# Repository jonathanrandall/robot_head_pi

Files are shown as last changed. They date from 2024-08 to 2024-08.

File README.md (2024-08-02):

# robot_head_pi
making a robot head with a raspberry pi insi
__Poppy Robot Project files__ 
[Poppy Robot Head stls from the poppy opens source project](https://github.com/poppy-project/Poppy-eva-head-design) <br/>

### Parts list:

- __Servo and servo mount__ 
[Cheap Ali express servos](https://www.aliexpress.com/w/wholesale-servo-25kg.html?spm=a2g0o.productlist.search.0)  and 
[servo pan tilt](https://www.aliexpress.com/w/wholesale-servo-pan-tilt-MG995-MG996.html?spm=a2g0o.productlist.search.0) <br/>
- __Raspberry Pi 4__ <br/>
- __90 degree USB C adapter to power pi__
[90 Degree Right Angle USB-C Male to USB-C Female Adapter](https://www.amazon.com.au/dp/B0B2NJ3P3L) <br/>
- __Stereo Camera__
I used [this one](https://www.amazon.com.au/Synchronized-Stereo-USB-Camera-Industrial/dp/B07R8LQKV4) from Amazon but shop around.<br/>
- __Arducam TOF camera__ <br/>
- __breadboard__ (just broke off the side for the 5v and earth rail) <br/>
- __perf board__ <br/>
- __2 x white leds__ (but you can use any colour you like) <br/>
- __2 x 220 ohm resistors__
- __tiny cylinder magnets__ I used these ones [from Amazon](https://www.amazon.com.au/dp/B0CM3KX5BC)

### Instructions
#### Step 1:
Mound the stereo camera, the time of flight camera and the leds on the pef board. 
The LEDs are should be in series with 220 ohm resistors and connected to pins 17 and 26 on the pi. I use 220 ohms because the pi gives 3.3 volts. Also, I drilled 2.5mm holes to mount the electronics on the perf board.
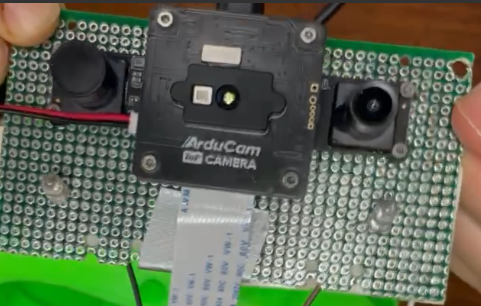
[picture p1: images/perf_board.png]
perf board


#### Step 2:
Print the following three robot head pieces from the Poppy Robot Project files listed above. [Poppy Robot Head](https://github.com/poppy-project/Poppy-eva-head-design) <br/>
__The work for this was done by 3 students of the ENSAM Bachelor of technology at Bordeaux, France: Damien MARTY, Clément GEA and Éléa CHARPNTIER, under the supervison of Jean-Luc CHARLES and Cécile DELARUE, professors at ENSAM Bordeaux.__ I have included the STL files in this repo (in the directory STL), just incase they become unavaiable on the original repo. <br/>
1. The eva_head_frontBottom
2. The head_RPi4Support
3. The head_top-part

They also provide some connectors to attach the tft for the face, but I'm using a pef board instead of a tft, so I just used hot glue. 

#### Step 3:
This is where my design differs from the original design.
Print the servo_head_connection-Body_v2.stl file. This is used to connect the head to the serov pan-tilt. I've also included the freecad file incase you want to adjust the position of the holes. It uses m2 screws. The original project has the head mounted directly to dynamixel servos, but the dynamixel servos were a bit expensive for me, so I went with the cheap ones. Although, with servos you do get what you pay for.
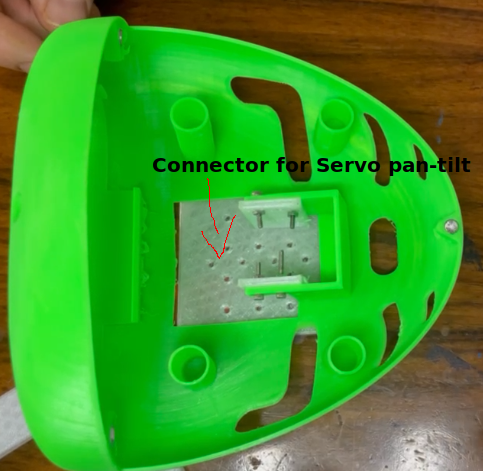
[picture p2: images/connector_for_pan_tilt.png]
connector for pan tilt


### Step 4:
Build the servo pan-tilt. See for example [https://youtu.be/3_fsS4YQ5Aw?si=ct7GD8LKidqGTTAt](https://youtu.be/3_fsS4YQ5Aw?si=ct7GD8LKidqGTTAt)

### Step 5:
Assemble printed files and push magnets into divets (see steps in original project as well). 
1. Connect the +ve of the LED & resistors to pins 17 and 26 of the pi and the -ve to earth. I soldered on some dupont female jumper wires.
2. Connect the servo pan tilt to the bottom of the head.
3. Connect the servo data (middle) wires to pins 18 and 27 of the pi.
4. Connect the servo +ve and -ve to the plus 5v and earth on the breadboard rail (see photo).
5. Connect the earth of the breadboard rail to one of the earths of the pi.
6. Place the perfboard in the face opening of the printed front of the head. You can cut this down to size. I used hot glue for this.
7. Connect the Arducam TOF camera to the pi camera input.
8. Connect the stereo camera to the usb pi input.

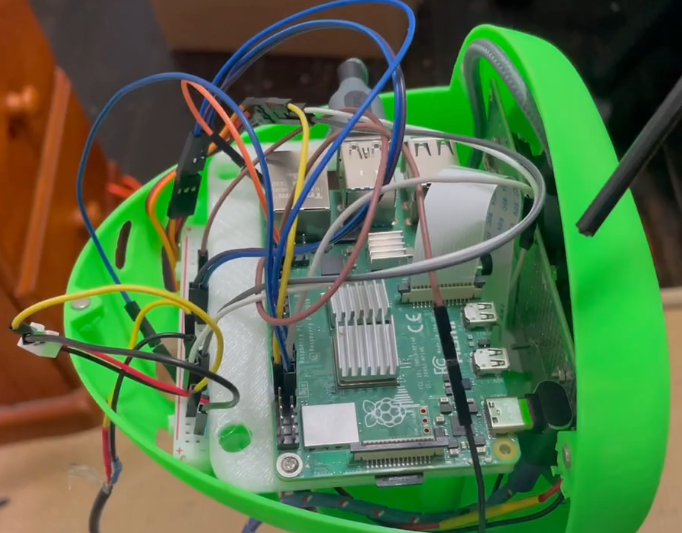
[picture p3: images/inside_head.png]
inside the head


### Step 6:
Put the back on and mount on neck. I used a piece of actobotics channel with a pillow mount that I had lying around. This has since been replaced by U-channel, which you can get from serocity or gobilda. But you can just use whatever you have lying around, whether it's an old piece of aluminium extrusion from a 3d printer or even a chari leg.

### Step 7:
Get the code running.
1. Install the ArducamDepthCamera. If you are on bookwork, you should do this in a virtual environment. To get the camera working see Arducam getting started [https://docs.arducam.com/Raspberry-Pi-Camera/Tof-camera/Getting-Started/](https://docs.arducam.com/Raspberry-Pi-Camera/Tof-camera/Getting-Started/) and
[Arducam github](https://github.com/ArduCAM/Arducam_tof_camera)
2. Note, for the getting started code from Arducam, the index of the camera is set to 0. Since we are using two cameras we need to find the index at run time. There is a function in my python code for this.
3. To run my code, make sure the python file ```robot_head.py``` and the html file ```index.html``` are in the same directory.
4. Since the code serves a webpage, you need to run with sudo, but for some reason, at least for me, I had to qualify the python3 command with the full path of the virtual environment. So I had to type ```sudo path/to/venv/python3 robot_head.py```
5. Go to the pi ip in your browser. I tested this from a computer and a tablet but not a smart phone. You can find the ip by typing ifconfig, or you can just enter the piname.local.

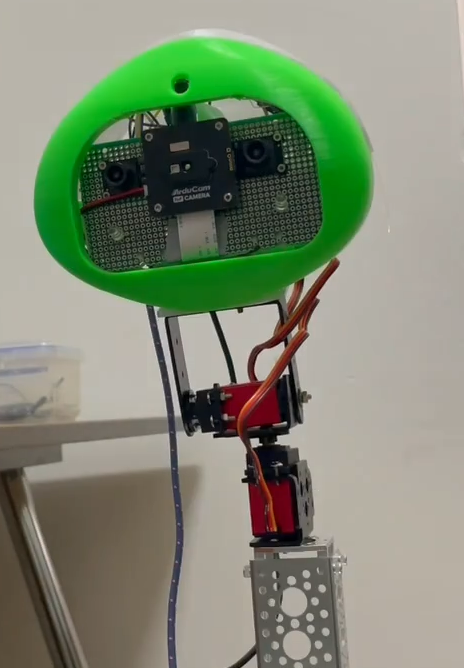
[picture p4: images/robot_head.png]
pi head


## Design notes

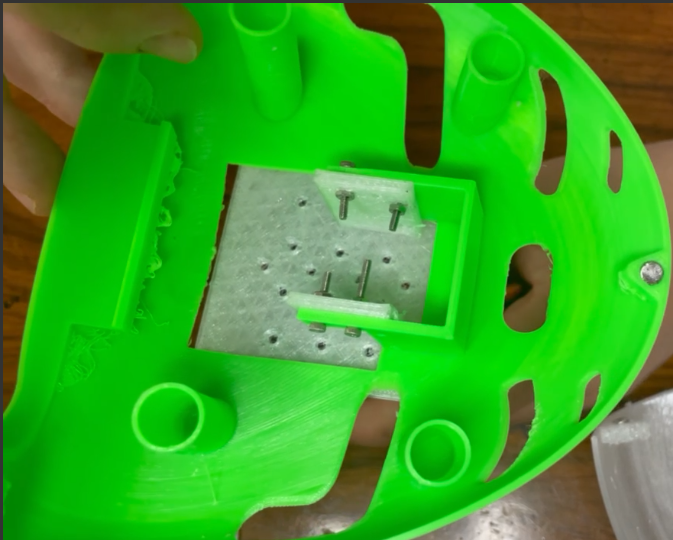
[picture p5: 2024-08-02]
images/Screenshot.png

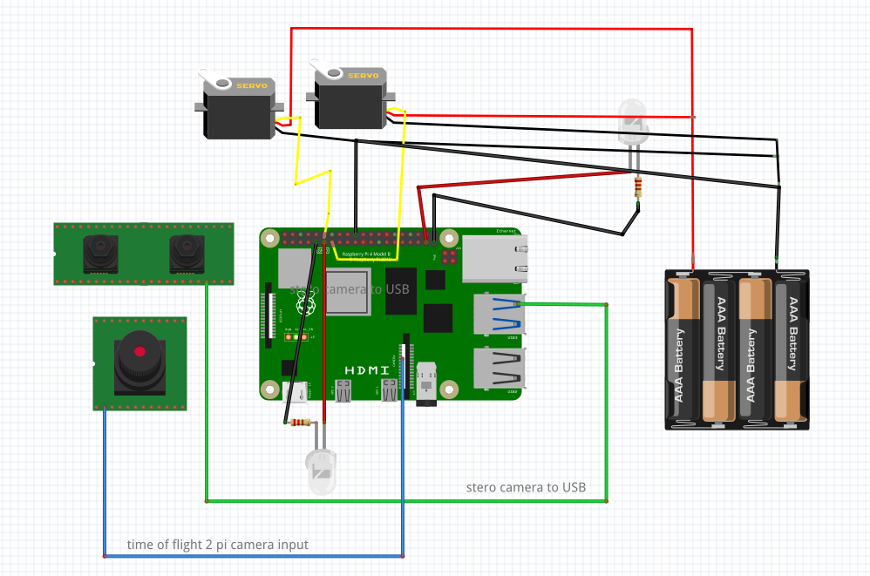
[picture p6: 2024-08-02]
circuit_diagrams/fritzing_circuit.png

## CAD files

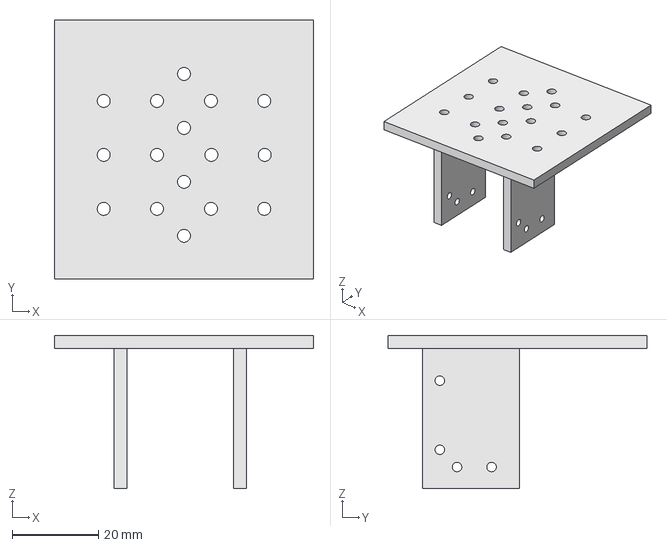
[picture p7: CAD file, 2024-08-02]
servo_mount_3d_print/servo_head_connection.FCStd
60.0 x 60.0 x 35.5 mm

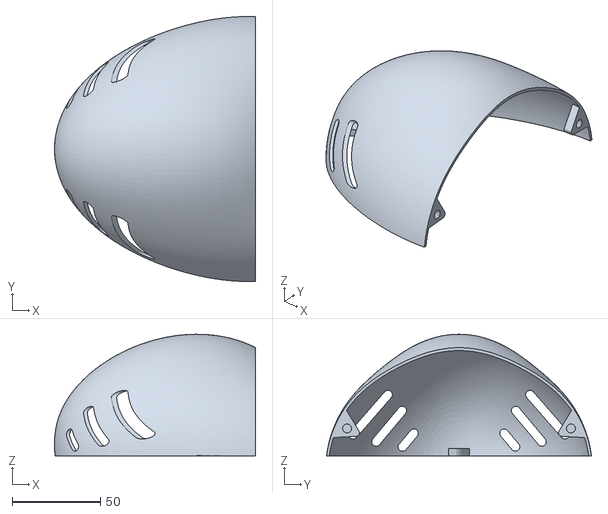
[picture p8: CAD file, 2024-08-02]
servo_mount_3d_print/STL/eva_head_top-part.stl
114.1 x 150.3 x 68.9

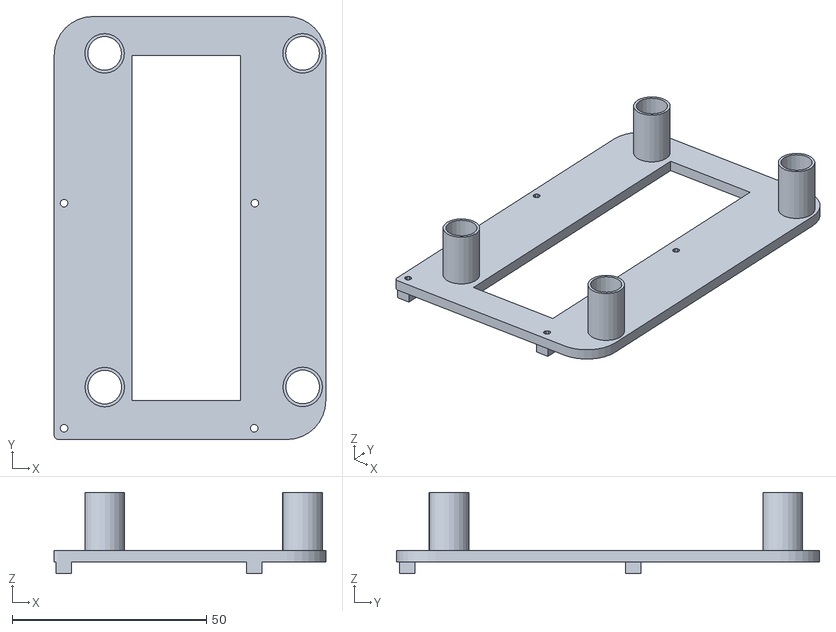
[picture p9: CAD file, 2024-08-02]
servo_mount_3d_print/STL/eva_head_RPi4Support.stl
70.0 x 109.0 x 21.0

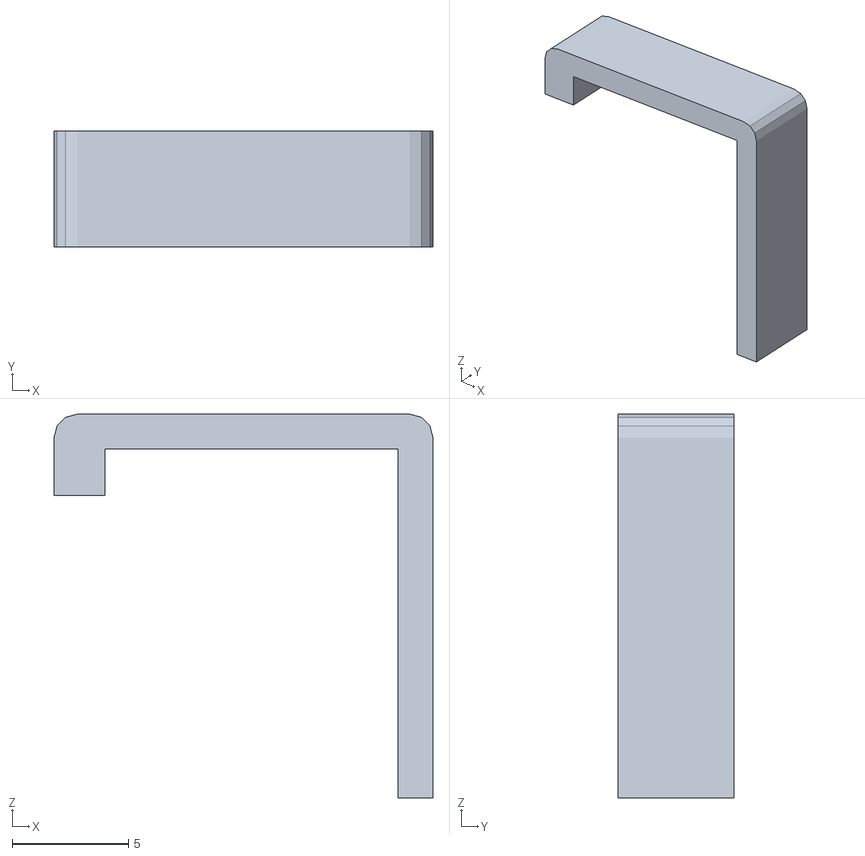
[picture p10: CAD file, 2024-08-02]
servo_mount_3d_print/STL/eva_head_lock-part.stl
16.3 x 5.00 x 16.5

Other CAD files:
servo_mount_3d_print/servo_head_connection-Body_v2.stl

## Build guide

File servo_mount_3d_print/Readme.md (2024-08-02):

The STL directory contains the files from the [eva-head poppy robot project](https://github.com/poppy-project/Poppy-eva-head-design).

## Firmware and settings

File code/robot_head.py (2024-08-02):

from http.server import BaseHTTPRequestHandler, HTTPServer
from socketserver import ThreadingMixIn
import cv2
import threading
import time
from collections import deque
import RPi.GPIO as GPIO
import urllib.parse
import sys

import ArducamDepthCamera as ac
import numpy as np


MAX_DISTANCE = 4

# Set up GPIO
LED_PIN = 17
LED_PIN2 = 26
SERVO_PIN_HORIZONTAL = 27
SERVO_PIN_VERTICAL = 18

GPIO.setmode(GPIO.BCM)
# GPIO.cleanup(LED_PIN)
GPIO.setup(LED_PIN, GPIO.OUT)
GPIO.setup(LED_PIN2, GPIO.OUT)
GPIO.setup(SERVO_PIN_HORIZONTAL, GPIO.OUT)
GPIO.setup(SERVO_PIN_VERTICAL, GPIO.OUT)

GPIO.output(LED_PIN, GPIO.LOW)
GPIO.output(LED_PIN2, GPIO.LOW)

# Set up PWM for servo control
servo_horizontal = GPIO.PWM(SERVO_PIN_HORIZONTAL, 50)  # 50Hz PWM frequency
servo_vertical = GPIO.PWM(SERVO_PIN_VERTICAL, 50)      # 50Hz PWM frequency
servo_horizontal.start(0)
servo_vertical.start(0)
import subprocess

# cam = ac.ArducamCamera()
# if cam.open(ac.TOFConnect.CSI,0) != 0 :
#     print("initialization failed")
# if cam.start(ac.TOFOutput.DEPTH) != 0 :
#     print("Failed to start camera")
# cam.setControl(ac.TOFControl.RANG,MAX_DISTANCE)
# frame_tmp = cam.requestFrame(200)
# depth_buf = frame_tmp.getDepthData()
# amplitude_buf = frame_tmp.getAmplitudeData()
# cam.releaseFrame(frame_tmp)
# amplitude_buf*=(255/1024)
# amplitude_buf = np.clip(amplitude_buf, 0, 255)
# result_image = process_frame(depth_buf,amplitude_buf)
# cv2.imshow("preview",result_image)

# key = cv2.waitKey(1)
# if key == ord("q"):
#     exit_ = True
#     cam.stop()
#     cam.close()
    
def process_frame(depth_buf: np.ndarray, amplitude_buf: np.ndarray) -> np.ndarray:
        
    depth_buf = np.nan_to_num(depth_buf)

    amplitude_buf[amplitude_buf<=7] = 0
    amplitude_buf[amplitude_buf>7] = 255

    depth_buf =(1 - (depth_buf/MAX_DISTANCE)) * 255
    depth_buf = np.clip(depth_buf, 0, 255)
    result_frame = depth_buf.astype(np.uint8)  & amplitude_buf.astype(np.uint8)
    return result_frame 
class ArduCamCam(threading.Thread):
    def __init__(self):
        threading.Thread.__init__(self)
        cam = ac.ArducamCamera()
        camIDx = int(find_webcam_index("unicam"))
        if cam.open(ac.TOFConnect.CSI,camIDx) != 0 :
            print("initialization failed")
        if cam.start(ac.TOFOutput.DEPTH) != 0 :
            print("Failed to start camera")
        cam.setControl(ac.TOFControl.RANG,MAX_DISTANCE)
        self.cam = cam
        self.running = True
        self.frame_queue = deque(maxlen=1)

    def run(self):
        while self.running:
            frame = self.cam.requestFrame(200)
            
            if frame is not None:
                depth_buf = frame.getDepthData()
                amplitude_buf = frame.getAmplitudeData()
                self.cam.releaseFrame(frame)

                amplitude_buf *= (255 / 1024)
                amplitude_buf = np.clip(amplitude_buf, 0, 255)
                result_image = process_frame(depth_buf, amplitude_buf)
                
                ret, jpeg = cv2.imencode('.jpg', result_image)
                if ret:
                    self.frame_queue.append(jpeg.tobytes())
                else:
                    print("Failed to encode frame as JPEG")
            else:
                print("Failed to deque buffer")
            
            time.sleep(0.01)

    def get_frame(self):
        if self.frame_queue:
            return self.frame_queue[-1]
        else:
            return None

    def stop(self):
        self.running = False
        self.cam.stop()
        self.cam.close()



def find_webcam_index(device_name):
    command = "v4l2-ctl --list-devices"
    output = subprocess.check_output(command, shell=True, text=True)
    devices = output.split('\n\n')
    
    for device in devices:
        if device_name in device:
            lines = device.split('\n')
            for line in lines:
                if "video" in line:
                    parts = line.split()
                    for part in parts:
                        if part.startswith('/dev/video'):
                            print(part)
                            return (part[10:])


def set_servo_angle(servo, angle):
    duty_cycle = angle / 18 + 2
    # GPIO.output(servo, True)
    servo.ChangeDutyCycle(duty_cycle)
    time.sleep(0.5)
    # GPIO.output(servo, False)
    servo.ChangeDutyCycle(0)

# Camera feed class
class CameraFeed(threading.Thread):
    def __init__(self):
        threading.Thread.__init__(self)
        webcam_index = int(find_webcam_index('3D USB'))
        self.camera = cv2.VideoCapture(webcam_index, apiPreference=cv2.CAP_V4L2)
        self.running = True
        self.frame_queue = deque(maxlen=1)

    def run(self):
        while self.running:
            success, frame = self.camera.read()
            if not success:
                break
            else:
                ret, jpeg = cv2.imencode('.jpg', frame)
                self.frame_queue.append(jpeg.tobytes())
                time.sleep(0.01)

    def get_frame(self):
        if self.frame_queue:
            return self.frame_queue[-1]
        else:
            return None

    def stop(self):
        self.running = False
        self.camera.release()

# Initialize CameraFeed instance
camera_feed = CameraFeed()
camera_feed.start()

cam_tof_feed = ArduCamCam()
cam_tof_feed.start()

# HTTP request handler
class RequestHandler(BaseHTTPRequestHandler):
    def do_GET(self):
        try:
            if self.path == '/':
                self.send_response(200)
                self.send_header('Content-type', 'text/html')
                self.end_headers()
                with open('index.html', 'rb') as f:
                    self.wfile.write(f.read())
            if self.path == '/led/on':
                GPIO.output(LED_PIN, GPIO.HIGH)
                GPIO.output(LED_PIN2, GPIO.HIGH)
                self.send_response(200)
                self.send_header('Content-type', 'text/plain')
                self.end_headers()
                self.wfile.write(b'LED turned on')
            elif self.path == '/led/off':
                GPIO.output(LED_PIN, GPIO.LOW)
                GPIO.output(LED_PIN2, GPIO.LOW)
                self.send_response(200)
                self.send_header('Content-type', 'text/plain')
                self.end_headers()
                self.wfile.write(b'LED turned off')
            elif self.path == '/video_feed2':
                self.send_response(200)
                self.send_header('Content-type', 'multipart/x-mixed-replace; boundary=frame')
                self.end_headers()

                while True:
                    try:
                        frame = camera_feed.get_frame()
                        # print('video feed2')
                        if frame is None:
                            continue

                        self.wfile.write(b'--frame\r\n')
                        self.send_header('Content-type', 'image/jpeg')
                        self.end_headers()
                        self.wfile.write(frame)
                        self.wfile.write(b'\r\n')

                        time.sleep(0.1)  # Adjust frame rate control if needed
                    except Exception as e:
                        break
            
            elif self.path == '/video_feed1':
                self.send_response(200)
                self.send_header('Content-type', 'multipart/x-mixed-replace; boundary=frame')
                self.end_headers()

                while True:
                    try:
                        frame2 = cam_tof_feed.get_frame() #cam.requestFrame(200)
                        if frame2 is None:
                            continue

                        self.wfile.write(b'--frame\r\n')
                        self.send_header('Content-type', 'image/jpeg')
                        self.end_headers()
                        self.wfile.write(frame2)
                        self.wfile.write(b'\r\n')
                                                
                        # if frame2 != None :
                        #     print("getting frame")
                        #     depth_buf = frame2.getDepthData()
                        #     print('here now 2')
                        #     amplitude_buf = frame2.getAmplitudeData()
                        #     cam.releaseFrame(frame2)
                            
                        #     amplitude_buf*=(255/1024)
                        #     amplitude_buf = np.clip(amplitude_buf, 0, 255)
                        #     result_image = process_frame(depth_buf,amplitude_buf)
                        #     print('here now 3')
                        #     ret, jpeg2 = cv2.imencode('.jpg', result_image)
                        # # frame = cam_tof_feed.get_frame()
                        # # if frame is None:
                        # #     continue
                        
                        # self.wfile.write(b'--frame\r\n')
                        # self.send_header('Content-type', 'image/jpeg')
                        # self.end_headers()
                        # self.wfile.write(jpeg2.tobytes())
                        # self.wfile.write(b'\r\n')
                        # print('here now 3')
                        time.sleep(0.1)  # Adjust frame rate control if needed
                    except Exception as e:
                        print('exception')
                        break
            elif self.path.startswith('/servo/horizontal'):
                query = urllib.parse.urlparse(self.path).query
                params = urllib.parse.parse_qs(query)
                angle = int(params.get('value', [0])[0])
                # print(angle)
                set_servo_angle(servo_horizontal, angle)
                self.send_response(200)
                self.send_header('Content-type', 'text/plain')
                self.end_headers()
                self.wfile.write(b'Horizontal servo angle updated')
            elif self.path.startswith('/servo/vertical'):
                query = urllib.parse.urlparse(self.path).query
                params = urllib.parse.parse_qs(query)
                angle = int(params.get('value', [0])[0])
                set_servo_angle(servo_vertical, angle)
                self.send_response(200)
                self.send_header('Content-type', 'text/plain')
                self.end_headers()
                self.wfile.write(b'Vertical servo angle updated')
        except IOError:
            print(self.path)
            self.send_error(404, 'File Not Found: %s' % self.path)

# Threading mixin for concurrent HTTP server
class ThreadedHTTPServer(ThreadingMixIn, HTTPServer):
    pass

def run(server_class=ThreadedHTTPServer, handler_class=RequestHandler, port=80):
    server_address = ('', port)
    httpd = server_class(server_address, handler_class)
    print(f'Starting server on port {port}...')
    httpd.serve_forever()


if __name__ == '__main__':
    # cam = ac.ArducamCamera()
    # if cam.open(ac.TOFConnect.CSI,0) != 0 :
    #     print("initialization failed")
    # if cam.start(ac.TOFOutput.DEPTH) != 0 :
    #     print("Failed to start camera")
    # cam.setControl(ac.TOFControl.RANG,MAX_DISTANCE)
    try:
        run()
    except KeyboardInterrupt:
        try:
            # print('in interrupt')
            camera_feed.stop()
            # print('camera feed stopped')
            servo_vertical.stop()
            servo_horizontal.stop()
            # print('servo stopped')
        except Exception:
            pass
        GPIO.cleanup(LED_PIN)
        GPIO.cleanup(LED_PIN2)
        GPIO.cleanup(SERVO_PIN_HORIZONTAL)
        GPIO.cleanup(SERVO_PIN_VERTICAL)
        
